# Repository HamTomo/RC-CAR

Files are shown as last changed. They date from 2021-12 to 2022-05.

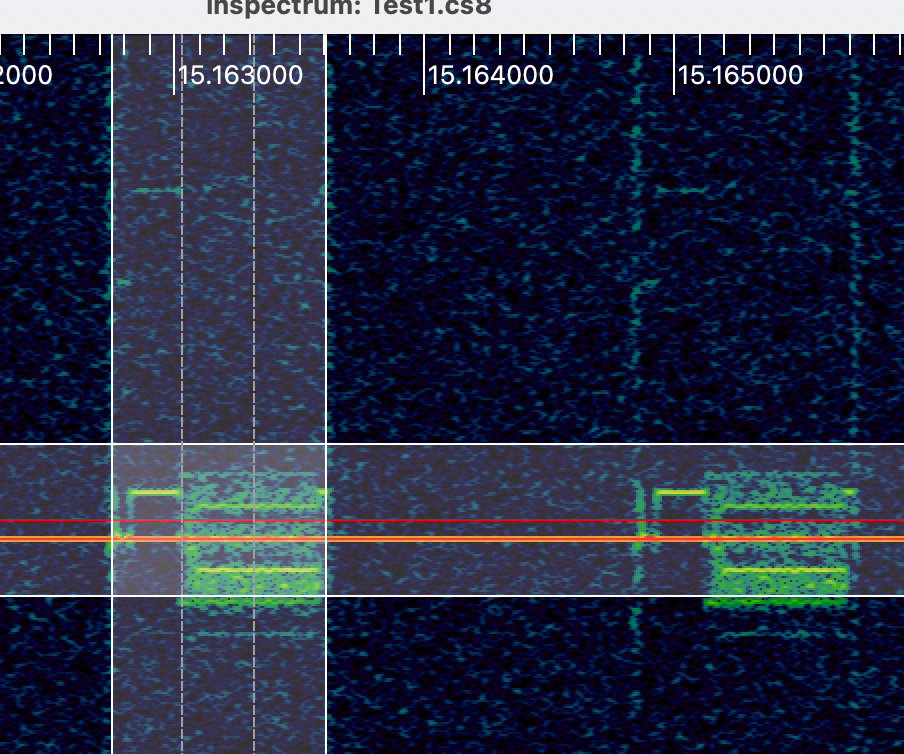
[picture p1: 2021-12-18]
Images/Analysis/Screenshot 2021-11-28 at 19.40.55.png

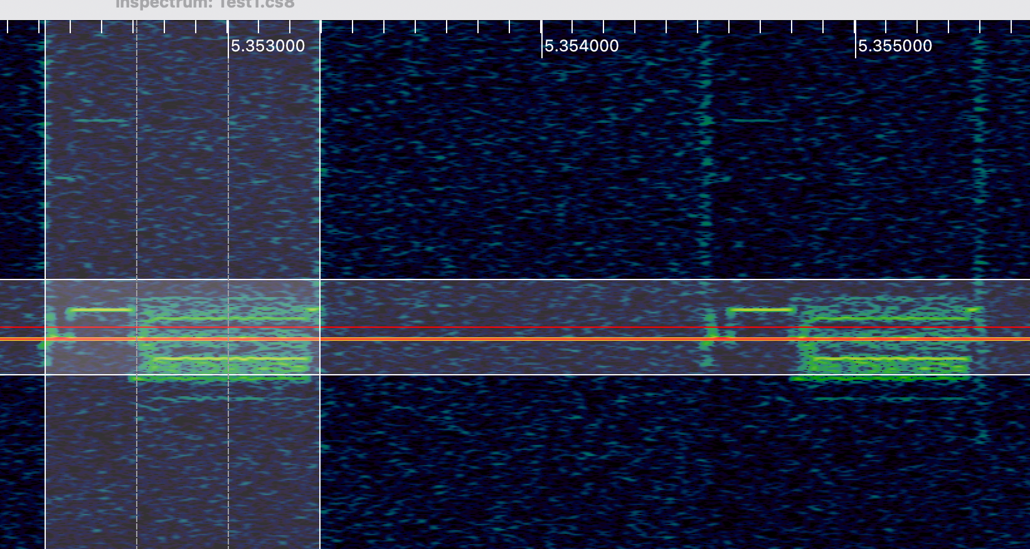
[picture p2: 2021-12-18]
Images/Analysis/Screenshot 2021-11-28 at 19.45.15.png

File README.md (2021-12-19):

# RC-CAR

RC Car Notes

------------------------------------------------------------
WIP:
-----
- Laptop driven TX
	+ Schematic
	+ Layout
- What is sent per TX switch?
	+
- Figure out why not pairing
	+ 

------------------------------------------------------------
To Do:
-----
- Identify TX/RX IC
- How does TX/RX pair?
- What is sent per TX switch?
	+ Confirm binary on/off at RX
- Layout PCBA
- ID repurpose points
- Laptop driven TX
	+ Mockup
- Measure Motor Series Resistance
- Measure components
- Platform characteristics
	- Acceleration
	- Turning Radius
	- Steering Motor Torque/Load Curves
	- Drive Motor Torque/Load Curves

------------------------------------------------------------

------------------------------------------------------------
Done:
-----
- Schematic Drawn
- EBoM First Pass
- Translate Motor Driver IC

------------------------------------------------------------

Inspectrum analysis

Signal 1
First instance start:		1.747s
Last instance start:		9.0616s
Time between instances:	25.36ms (Assume 25ms?)
No. of instances:			289
No. per press:			58

Instance Breakdown
2 blocks
1st 868ms
2nd 864ms
SS 2.108
3 symbols per block?
011

Signal 2
First instance start:		10.081s
Last instance start:		15.1627s
Time between instances:	25.392 

Instance Breakdown
2 blocks
1st 880us
2nd 880us
SS 2.01ms
3 symbols per block?
011

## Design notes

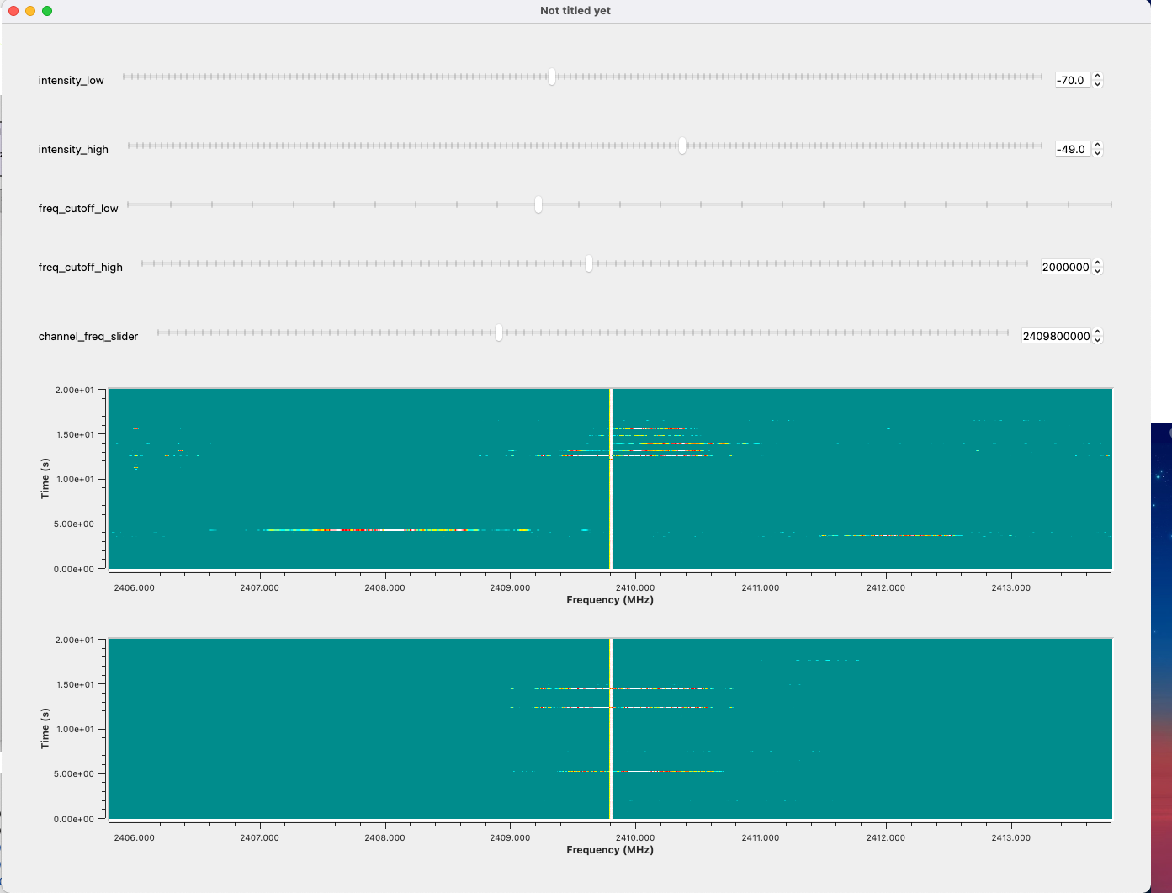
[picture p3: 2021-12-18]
Images/Analysis/Screenshot 2021-11-07 at 21.20.09.png

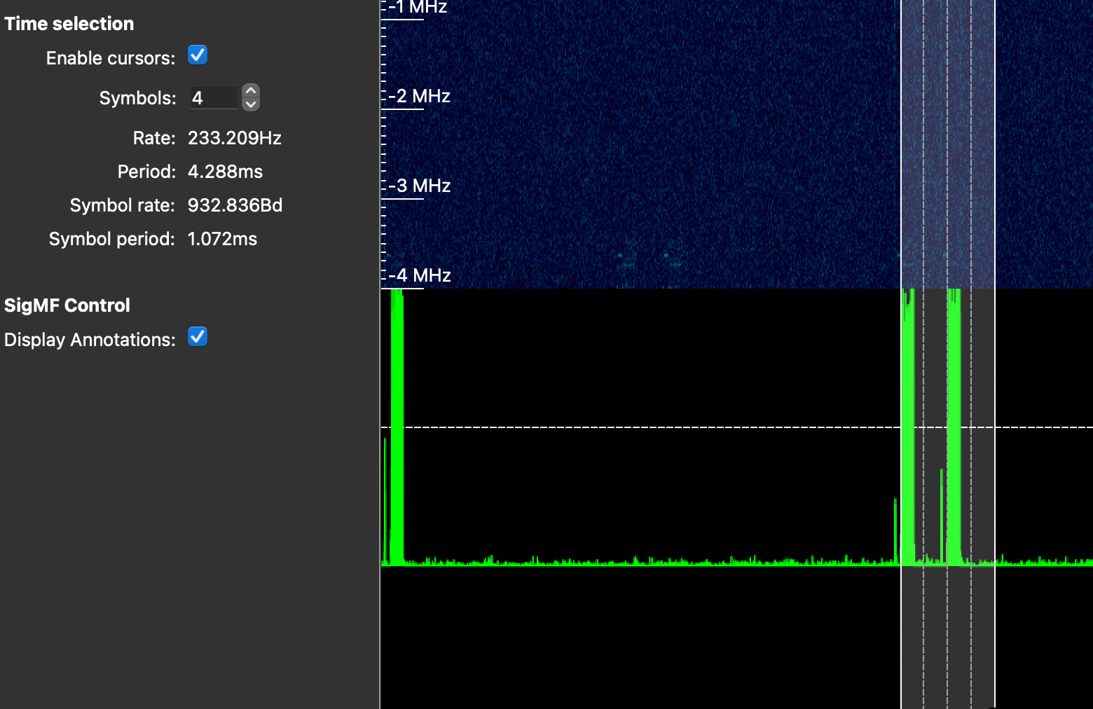
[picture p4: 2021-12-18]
Images/Analysis/Screenshot 2021-11-21 at 20.21.08.png

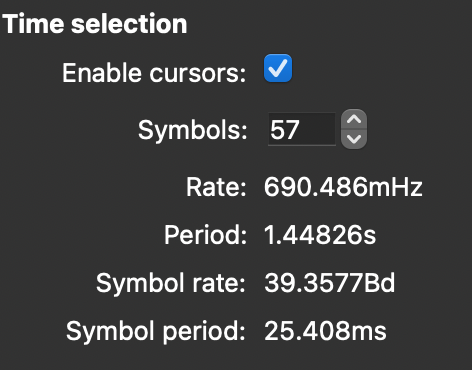
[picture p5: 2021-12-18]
Images/Analysis/Screenshot 2021-11-21 at 20.16.55.png

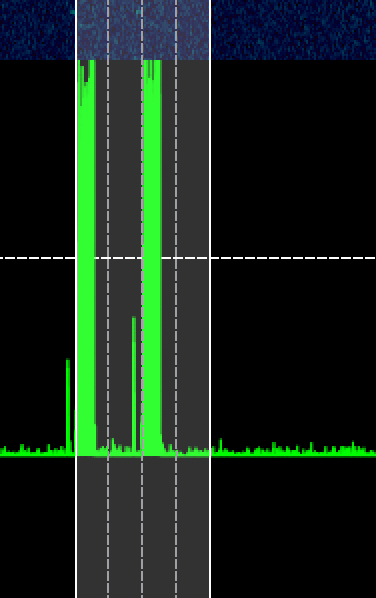
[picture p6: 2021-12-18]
Images/Analysis/Screenshot 2021-11-21 at 20.21.00.png

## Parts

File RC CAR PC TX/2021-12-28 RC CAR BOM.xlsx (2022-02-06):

Source: | /Users/hamish/Library/Mobile Documents/com~apple~CloudDocs/Projects/Active/RC-CAR/RC CAR PC TX/RC CAR.kicad_sch
Date: | Tuesday, 28 December 2021 at 15:26:19
Tool: | Eeschema (6.0.0-0)
Generator: | /Applications/KiCad/KiCad.app/Contents/SharedSupport/plugins/bom_csv_grouped_by_value_with_fp.py
Component Count: | 29
Ref | Qnty | Value | Cmp name | Footprint | Description | Vendor | Part identified | Footprint | Datasheet
AE1, | 1 | Antenna | Antenna | RF_Antenna:SZJJX_CAR_TX_2.4GHz_Left | Antenna |  | Yes | TBC | No
C1, C2, C3, | 3 | 1uF | C_Small | Capacitor_SMD:C_0603_1608Metric | Unpolarized capacitor, small symbol |  | Yes | Yes | Yes
C4, C5, C6, C7, | 4 | 22uF | C_Small | Capacitor_SMD:C_0603_1608Metric | Unpolarized capacitor, small symbol |  | Yes | Yes | Yes
D1, | 1 | LED | LED |  | Light emitting diode |  | Yes | TBC | Yes
R1, | 1 | 1k | R_Small_US | Resistor_SMD:R_0603_1608Metric | Resistor, small US symbol |  | Yes | Yes | Yes
R2, R3, R4, R5, | 4 | 10k | R_Small_US | Resistor_SMD:R_0603_1608Metric | Resistor, small US symbol |  | Yes | Yes | Yes
R6, | 1 | 10 | R_Small_US | Resistor_SMD:R_0603_1608Metric | Resistor, small US symbol |  | Yes | Yes | Yes
R7, | 1 | 100 | R_Small_US | Resistor_SMD:R_0603_1608Metric | Resistor, small US symbol |  | Yes | Yes | Yes
SW2, SW3, SW4, SW5, | 4 | SW_SPST | SW_SPST |  | Single Pole Single Throw (SPST) switch |  | Yes | Yes | Yes
TP1, | 1 | FORWARD | TestPoint | TestPoint:Test_Point_0805_2012Metric | test point |  | Yes | Yes | Yes
TP2, | 1 | LEFT | TestPoint | TestPoint:Test_Point_0805_2012Metric | test point |  | Yes | Yes | Yes
TP3, | 1 | REVERSE | TestPoint | TestPoint:Test_Point_0805_2012Metric | test point |  | Yes | Yes | Yes
TP4, | 1 | RIGHT | TestPoint | TestPoint:Test_Point_0805_2012Metric | test point |  | Yes | Yes | Yes
TP5, | 1 | 3V3 | TestPoint | TestPoint:Test_Point_0805_2012Metric | test point |  | Yes | Yes | Yes
TP6, | 1 | 3V0 | TestPoint | TestPoint:Test_Point_0805_2012Metric | test point |  | Yes | Yes | Yes
U1, | 1 | Conn_02x07_Counter_Clockwise | Conn_02x07_Counter_Clockwise | Package_SO:SOIC-14_3.9x8.7mm_P1.27mm | TX SOIC |  | Yes | Yes | No
U3, | 1 | Pico | Pico-MCU_RaspberryPi_and_Boards |  |  |  | Yes | TBC | Yes
Y1, | 1 | Crystal | Crystal | 4-SMD No Lead |  |  | Yes | Yes | Yes

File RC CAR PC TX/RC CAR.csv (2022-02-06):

Source: | /Users/hamish/Library/Mobile Documents/com~apple~CloudDocs/Projects/Active/RC-CAR/RC CAR PC TX/RC CAR.kicad_sch
Date: | Tuesday, 28 December 2021 at 15:26:19
Tool: | Eeschema (6.0.0-0)
Generator: | /Applications/KiCad/KiCad.app/Contents/SharedSupport/plugins/bom_csv_grouped_by_value_with_fp.py
Component Count: | 29
Ref | Qnty | Value | Cmp name | Footprint | Description | Vendor
AE1, | 1 | Antenna | Antenna | RF_Antenna:SZJJX_CAR_TX_2.4GHz_Left | Antenna
C1, C2, C3, | 3 | 1uF | C_Small | Capacitor_SMD:C_0603_1608Metric | Unpolarized capacitor, small symbol
C4, C5, C6, C7, | 4 | 20uF | C_Small | Capacitor_SMD:C_0603_1608Metric | Unpolarized capacitor, small symbol
D1, | 1 | LED | LED | LED_THT:LED_D1.8mm_W3.3mm_H2.4mm | Light emitting diode
R1, | 1 | 1k | R_Small_US | Resistor_SMD:R_0603_1608Metric | Resistor, small US symbol
R2, R3, R4, R5, | 4 | 10k | R_Small_US | Resistor_SMD:R_0603_1608Metric | Resistor, small US symbol
R6, | 1 | 10 | R_Small_US | Resistor_SMD:R_0603_1608Metric | Resistor, small US symbol
R7, | 1 | 100 | R_Small_US | Resistor_SMD:R_0603_1608Metric | Resistor, small US symbol
SW2, SW3, SW4, SW5, | 4 | SW_SPST | SW_SPST | Button_Switch_THT:SW_TH_Tactile_Omron_B3F-10xx | Single Pole Single Throw (SPST) switch
TP1, | 1 | FORWARD | TestPoint | TestPoint:TestPoint_Pad_D2.0mm | test point
TP2, | 1 | LEFT | TestPoint | TestPoint:TestPoint_Pad_D2.0mm | test point
TP3, | 1 | REVERSE | TestPoint | TestPoint:TestPoint_Pad_D2.0mm | test point
TP4, | 1 | RIGHT | TestPoint | TestPoint:TestPoint_Pad_D2.0mm | test point
TP5, | 1 | 3V3 | TestPoint | TestPoint:TestPoint_Pad_D2.0mm | test point
TP6, | 1 | 3V0 | TestPoint | TestPoint:TestPoint_Pad_D2.0mm | test point
U1, | 1 | Conn_02x07_Counter_Clockwise | Conn_02x07_Counter_Clockwise | Package_SO:SOIC-14_3.9x8.7mm_P1.27mm | Generic connector, double row, 02x07, counter clockwise pin numbering scheme (similar to DIP packge numbering), script generated (kicad-library-utils/schlib/autogen/connector/)
U3, | 1 | Pico | Pico-MCU_RaspberryPi_and_Boards | Connector_PinSocket_2.54mm:PinSocket_2x20_P2.54mm_Vertical_SMD
Y1, | 1 | Crystal | Crystal | Crystal:Crystal_HC18-U_Vertical | Two pin crystal

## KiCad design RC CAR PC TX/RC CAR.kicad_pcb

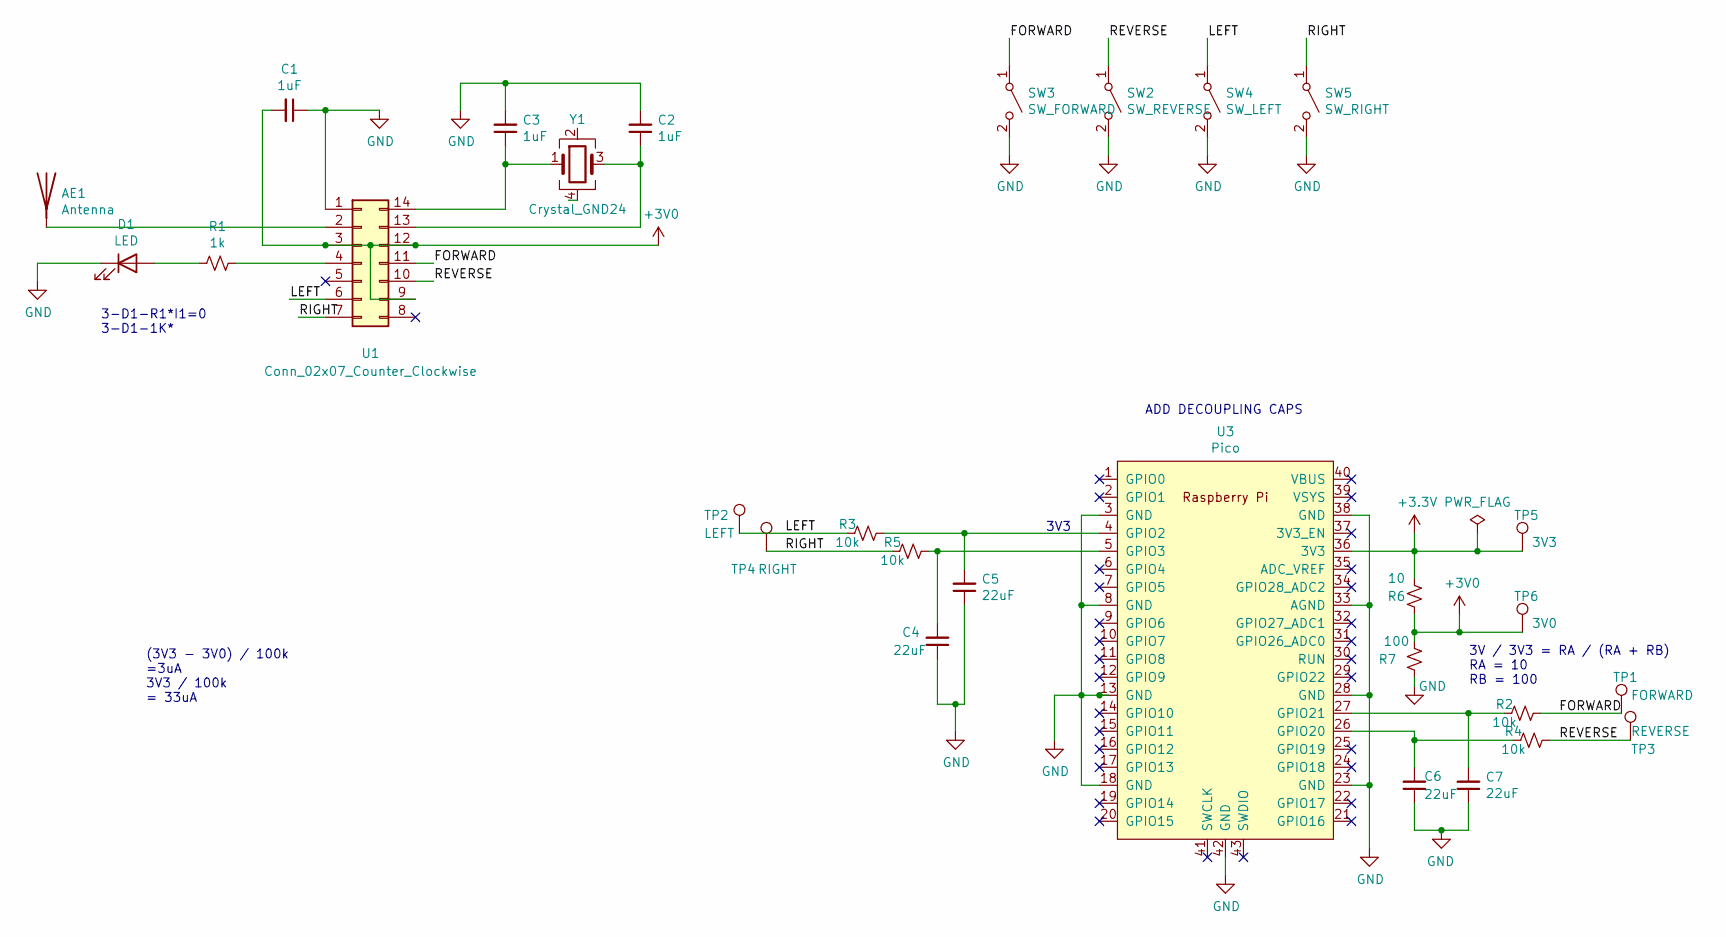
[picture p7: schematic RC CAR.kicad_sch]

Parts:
AE1: Antenna; SZJJX_CAR_TX_2.4GHz_Left
C1, C2, C3: 1uF; C_0603_1608Metric
C4, C5, C6, C7: 22uF; C_0603_1608Metric
D1: LED; DS144_Luxeon_LED_SMD_1CAT
R1: 1k; R_0603_1608Metric
R2, R3, R4, R5: 10k; R_0603_1608Metric
R6: 10; R_0603_1608Metric
R7: 100; R_0603_1608Metric
SW2: SW_REVERSE; RC TLS TacSwitch
SW3: SW_FORWARD; RC TLS TacSwitch
SW4: SW_LEFT; RC TLS TacSwitch
SW5: SW_RIGHT; RC TLS TacSwitch
TP1: FORWARD; Test_Point_0805_2012Metric
TP2: LEFT; Test_Point_0805_2012Metric
TP3: REVERSE; Test_Point_0805_2012Metric
TP4: RIGHT; Test_Point_0805_2012Metric
TP5: 3V3; Test_Point_0805_2012Metric
TP6: 3V0; Test_Point_0805_2012Metric
U1: Conn_02x07_Counter_Clockwise; SOIC-14_3.9x8.7mm_P1.27mm
U3: Pico; Pico_Pi_Connector
Y1: Crystal_GND24; Crystal_SMD_SeikoEpson_FA238V-4Pin_3.2x2.5mm

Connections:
+3V0: C1.2, R6.1, R7.2, TP6.1, U1.3, U1.9, U1.12
+3V3: R6.2, TP5.1, U3.36 (3V3)
/FORWARD: R2.1, SW3.1 (A), TP1.1, U1.11
/LEFT: R3.2, SW4.1 (A), TP2.1, U1.6
/REVERSE: R4.1, SW2.1 (A), TP3.1, U1.10
/RIGHT: R5.2, SW5.1 (A), TP4.1, U1.7
GND: C1.1, C2.2, C3.2, C4.1, C5.1, C6.1, C7.1, D1.1 (K), R7.1, SW2.2 (B), SW3.2 (B), SW4.2 (B), SW5.2 (B), U1.1, U3.3 (GND), U3.8 (GND), U3.13 (GND), U3.18 (GND), U3.23 (GND), U3.28 (GND), U3.33 (AGND), U3.38 (GND), U3.42 (GND)
unnamed: AE1.1 (A), U1.2
unnamed: C2.1, U1.13, Y1.3
unnamed: C3.1, U1.14, Y1.1
unnamed: C4.2, R5.1, U3.5 (GPIO3)
unnamed: C5.2, R3.1, U3.4 (GPIO2)
unnamed: D1.2 (A), R1.2
unnamed: R1.1, U1.4
unnamed: C6.2, R4.2, U3.26 (GPIO20)
unnamed: C7.2, R2.2, U3.27 (GPIO21)

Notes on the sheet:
3V / 3V3 = RA / (RA + RB) RA = 10 RB = 100
3V3
ADD DECOUPLING CAPS
(3V3 - 3V0) / 100k =3uA 3V3 / 100k = 33uA
3-D1-R1*I1=0 3-D1-1K*

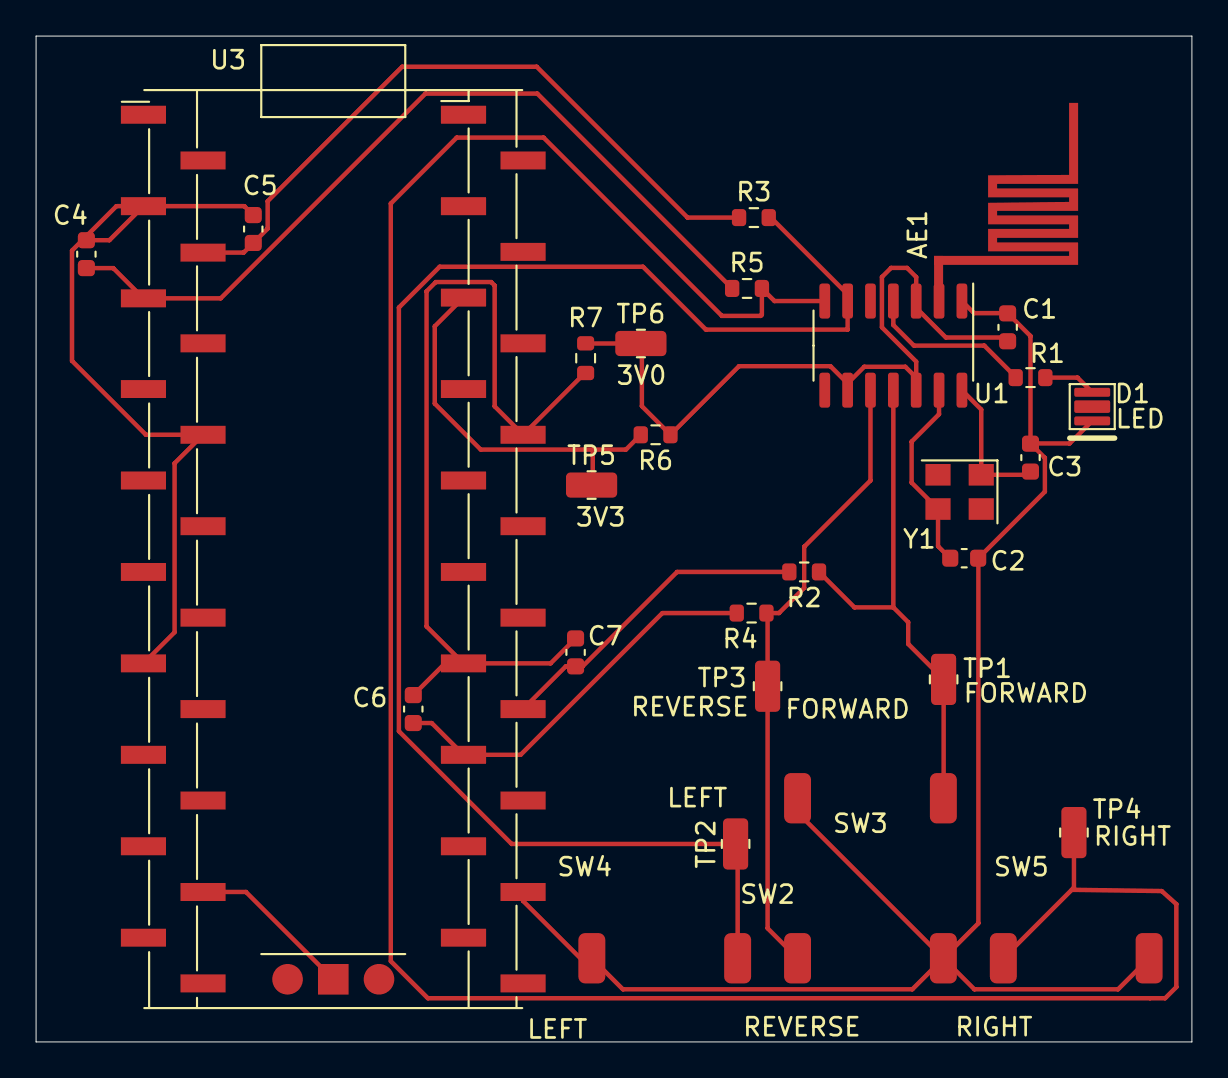
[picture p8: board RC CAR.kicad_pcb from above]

Board: 2 copper layers, 64.2 x 55.9 mm, 29 parts (0 on the bottom side), 16 nets.

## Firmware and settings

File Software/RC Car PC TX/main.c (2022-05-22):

/******************************************
*	
* 	main.c for RC-CAR PC TX
* 
* 	Version:	1.0
* 	Date:		2022-05-22
* 	Author:		Hamish T
* 
*	Enable GPIO on pins
*	GP0, GP1, GP2, GP3
*	Output, Default set high
*	
*	REVERSE	SW2		GPIO2
* 	FORWARD	SW3		GPIO3
* 	LEFT	SW4		GPIO20
* 	RIGHT	SW5		GPIO21
*
*
*******************************************/

#include <stdio.h>
#include "pico/stdlib.h"
#include "hardware/gpio.h"
#include "pico/binary_info.h"
//Full relative address /../pico-sdk/src/common/pico_stdlib/include/pico/stdlib.h

const uint LED_PIN = 25;
const uint REVERSE = 20;
const uint FORWARD = 21;
const uint LEFT = 2;
const uint RIGHT = 3;

void test_drive(void)
{
	/*Cycle through each direction*/
	//FORWARD
	puts("FORWARD\n");
	gpio_put(FORWARD, 0);
	sleep_ms(250);
	gpio_put(FORWARD, 1);
	sleep_ms(1000);

	//REVERSE
	puts("REVERSE\n");
	gpio_put(REVERSE, 0);
	sleep_ms(250);
	gpio_put(REVERSE, 1);
	sleep_ms(1000);

	//LEFT
	puts("LEFT\n");
	gpio_put(LEFT, 0);
	sleep_ms(250);
	gpio_put(LEFT, 1);
	sleep_ms(1000);

	//RIGHT
	puts("RIGHT\n");
	gpio_put(RIGHT, 0);
	sleep_ms(250);
	gpio_put(RIGHT, 1);
	sleep_ms(1000);
}

void gpio_init_all(void)
{
	stdio_init_all();

	gpio_init (LED_PIN);
	gpio_init (FORWARD);
	gpio_init (REVERSE);
	gpio_init (LEFT);
	gpio_init (RIGHT);

	//set outputs
  	gpio_set_dir(LED_PIN, GPIO_OUT);
	gpio_set_dir(FORWARD, GPIO_OUT);
	gpio_set_dir(REVERSE, GPIO_OUT);
	gpio_set_dir(RIGHT, GPIO_OUT);
	gpio_set_dir(LEFT, GPIO_OUT);

	//Set starting output direction
	gpio_put(FORWARD, 1);
	gpio_put(REVERSE, 1);
	gpio_put(LEFT, 1);
	gpio_put(RIGHT, 1);
	gpio_put(LED_PIN, 1);

}



int main()
{
   bi_decl(bi_program_description("This is a RC Car test binary."));
   bi_decl(bi_1pin_with_name(LED_PIN, "On-board LED"));

   gpio_init_all();  



   while (true)
   {
   		gpio_put(LED_PIN, 1);
		sleep_ms(250);
		gpio_put(LED_PIN, 0);
		sleep_ms(250);
		puts("Blink Blink\n");
		gpio_put(LED_PIN, 1);
		sleep_ms(250);
		gpio_put(LED_PIN, 0);
		sleep_ms(250);

		test_drive();
		sleep_ms(1000);

	}
}

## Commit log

2021-12-18 Files commit
    [RC CAR 3.sch, RC CAR.kicad_pcb, RC CAR.sch]
2022-02-06 Updated PCB layout for PCBA 2.0
    [RC CAR.kicad_pcb]
2022-02-13 Updated files
    [RC CAR.kicad_pcb]
2022-05-22 Test script that cycles through controller switches and outputs direction to serial
